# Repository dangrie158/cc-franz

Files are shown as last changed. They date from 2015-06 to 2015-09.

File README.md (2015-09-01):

#Camera Control 
##--> iPad controlled camera slider <--

<br /><br />
###Who we are
Hi, let’s introduce ourselves first: we are [Daniel Grießhaber](https://twitter.com/DanielGriehaber) and [Tobias Schneider](https://twitter.com/hpppxl), two master students (Computer Science and Media) of the Stuttgart Media University.

###TL;DR
Awesome, selfmade Camera Slider for ~180€ that can be controlled and programmed via an iPad app. If you read along you will find information on how to build one yourself!

###What this is
During the summer term of 2015 we developed a Camera Slider for controllable and repeatable time lapse and realtime shots. Since there are [already a couple DIY sliders](http://hackaday.com/2014/01/27/yet-another-diy-camera-slider/) out there, we wanted to give ours some special features to make it stick out from the masses:

###Awesome feature list:
#####2 motorized axis (linear movement and panning)
Most DIY Camera Sliders out there have only one remote axis. We have two (more is always better). ;-)
#####WiFi Access
Thanks to some recent development in WiFi integration we were able to add an iPad to control the Camera Slider.
#####iPad Control
There are two ways of controlling the Camera Slider. First of all, you can handle the slider via the live control and steer both axis independently. Furthermore, you can record your movement and save it for later playback.
 
Secondly, you can create simple scripts over an intuitive, graphical UI to program the slider for long duration shots (e.g. time lapse) with a slow, smooth and continuous movement that is repeatable until you are happy with the outcome.

## TOC

* [Mechanical Engineering](Slider/CAD/)
* [Electrical Engineering](Slider/Mainboard/)
* [ESP8266 WiFi Module](Slider/WiFi-Module/)
* [Microcontroller](Slider/Firmware/)

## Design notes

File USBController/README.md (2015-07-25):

# cc-franz
This is part of the CC-Franz Project

Implemented by Stefan Seibert at Stuttgart Media University in Summer 2015
as part of the class "Embedded Systems" from Thomas Maier.

You will find two subfolders:

/USB-Shield
This subfolder contains the AVR based project code to use the
USB Host Shield with MAX3421 chip in combination with a AVR
ATmega328p without the need of the Arduino Development Framework.
The Code can be compiled with AVR-GCC by using the provided makefile.
It is configured to send the Input Data of a HID Gamecontroller via UART

Files in USB_Shield originated or extended from Stefan Seibert, comments in files also:
/utils.h + /utils.c - For sending data or debug information via UART
/usb_wifi.cpp - main file, for initiation of USB Protocol and sending commands
/hidjoystickrptparser.h + /hidjoystickrptparser.cpp - modified and extended to handle input correctly

/WebSocket_Client
this is the firmware for a websocket client for the ESP8266 WIFI module
It needs the esp_open_sdk (https://github.com/pfalcon/esp-open-sdk) 
for being compiled correctly. It can be compiled to flash the ESP8266.
It is configured to send the via UART received USB Control Data 
as WebSocket Messages.

Files in WebSocket_Client originated from Stefan Seibert, comments in files also:
/user/user_main.c - firmware main file for creating a HTTP Server in ESP8266
/user/websocketd.h + /user/websocketd.c - For creating a Websocket Connection as Server extended
from a old version from Daniel Grießhaber where WebSocket worked as client not as server.

HID Based Game Controller
=====================

Used Data for Events:

X = 1 A = 2 B = 3 Y = 4  L = 5 R = 6 Select = 9 Start = 10
Kreuz Links: Z2 = 0 Kreuz Rechts: Z2 = 255 
Kreuz Oben: Rz = 0 Kreuz Unten: Rz = 255
Start = Rotation und Move auf 0 
Kreuz links/rechts = Move -/+ 
Kreuz hoch/runter = Rotation -/+  

A = Move Speed 255/8
B = Move Speed 255/2
Y = Rotate Speed 255/8
X = Rotate Speed 255

L = Speed -2 R = Speed +2

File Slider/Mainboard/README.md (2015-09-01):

###Electrical Engineering

#####BOM (What you need)

| Qty | Device | Package | Value  | Parts | Description |
|-----|---|---|---|---|---|
| 2 | A4988 | DIP | – | U3, U4 | |
| 1 | ¼W Resistor | 0207 | 100 kΩ | R15 | |
| 1 | Potentiometer | CA9V | 100 kΩ | R16 | |
| 8 | Ceramic Capacitor | C050 | 100 nF | C1, C2, C4, C5, C6, E13, E14, E15 | |
| 2 | Electrolytic Capacitor | CA9V | 100 µF | C4, C8 | |
| 5 | ¼W Resistor | 0207 | 100 Ω  | R3, R4, R10, R11, R12 | |
| 8 | ¼W Resistor | 0207 | 10 kΩ  | R1, R2, R5, R6, R7, R8, R9, R14 | |
| 2 | Electrolytic Capacitor | CA9V | 10 µF  | C3, C16 | |
| 1 | Power Check | – | – | JP1 | |
| 1 | Crystal Oscillator | HC49 | 16 MHz | Q1 | |
| 1 | Diode | DO41 | – | D2 | |
| 4 | Electrolytic Capacitor | CA9V | 1 µF | C9, C10, C11, C12 | |
| 2 | Ceramic Capacitor | C050 | 22 pF  | C17, C18 | |
| 1 | LM33CV | TO22 | – | IC2 | |
| 1 | 8705 | TO22 | – | IC1 | |
| 1 | Atmega328P | DIL28 | – | U1 | |
| 2 | BC337 | TO92 | – | T1, T2 | NPM Transistor |
| 1 | 2 Pole Connector | – | – | IROUT | |
| 1 | 3 Pole Connector | – | – | ENDSTOP | |
| 3 | 4 Pole Connector | – | – | MOT1, MOT2, RS232 | |
| 1 | 2x3 Pin Header | – | – | ICSP | |
| 2 | 3 Channel DIP switch | – | – | MSMOT1, MSMOT2 | |
| 1 | ESP8266 | – | – | U5 | |
| 1 | LM358 | DIL08 | – | IC3 | jelly bean Opamp |
| 1 | MAX232 | DIL16 | – | U2 | |
| 1 | 5mm LED | – | – | D1 | |
| 6 | Tactile Button | – | – | HOMING, LEFT, RIGHT, TILTCCW, TILTCW, RESET | |

Total costs for electrical parts: <br />
**~ 39,33€ + shipping fees**

#####Schematic
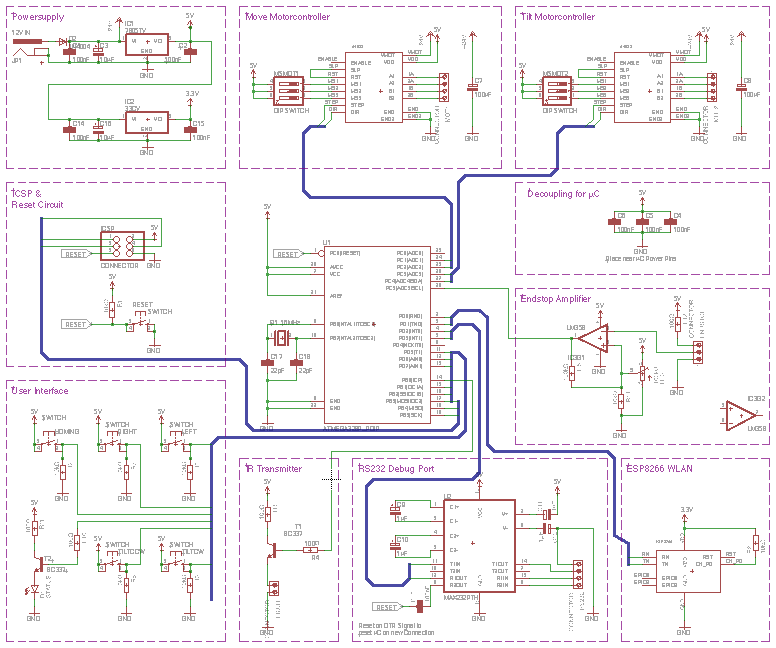
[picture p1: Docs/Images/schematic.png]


We designed the schematic modular to get a good overview of the whole system and work independently on single modules. 

######Microcontroller (not labeled, the part in the center)
For the brain of our slider we’ve chosen an ATMEGA 328 from Atmel. The reason for this simply was the huge amount of information and tutorials out there for this chip. This is the same chip you have on the Arduino Uno, the one you may have in your parts bin.  Just for kicks (and maybe also because this was a requirement by our lecturer) we did not use the Arduino bootloader or libraries and programmed the chip directly through the ISP interface. <br />
The chip has an whopping 32kB of Flash and 2kB of RAM.

######Powersupply
For the operation of the Camera Slider we need 3 different voltage rails: +12V for the motors, +5V for the microcontroller and as a main logic level and +3.3V as the WiFi module supply voltage.<br />
The +12V line is directly connected to the main power jack, which is supplied by an external plug pack. The +12V are only fed through a diode to protect the circuit from reverse polarization, which results in a small voltage drop of about the typical 0.7V.
For the +5V a linear 7805 voltage regulator was used, which turns any input voltage from +7V - +35V into a regulated +5V. The aforementioned is accomplished by burning all the extra energy and turning it into heat. During normal operation our slider consumes about 300mA on the +5V rail and therefore the energy of



heat needs to be dissipated. For that reason we attached a small heatsink to the voltage regulator. <br />
The 3.3V rail is also regulated by a linear regulator, but this time with another output voltage. The input voltage comes from the +5V line, which means that the 7805 needs to supply the current for the +3.3V rail as well. However, directly attaching the regulator to the 12V would mean that it needs to dissipate all the power down to the 3.3V, wich would result in a drop voltage of 12V - 3.3V = 8.7V. This way, the heat is spread across the two regulators.

######ICSP & Reset Circuit
The ICSP connector is needed to program the ATMEGA microcontroller. It is a simple SPI bus with power supply and a connection to the RESET pin of the controller. To flash the controller, the programmer needs to set the RESET pin low and therefore keeps the microcontroller in its reset state during the flashing process. To start the microcontroller, one needs to keep the RESET pin high. For this reason the RESET pin is connected to the 5V rail with a 10kΩ pull-up resistor. <br />
For manually resetting the controller, we also added a switch to pull the pin low. 

######Motor Controller (x2)
To drive the motors, we used 2 A4988 motor drivers. They handle all the complex driving and enable us to microstep the motors, which results in an up to 16x higher resolution to drive the motor. <br />
The microstepping setting is not subject to change during operation. However, to be able to set the bits manually we simply added a 3 pole DIP switch to each driver which allows us to change the setting after laying out the board.<br />
One could also hard-wire the setting in the same board layout by not populating the switches, but solder in the connections directly.
The microcontroller can make the motor step (or microstep) by toggling the STEP pin of the controller for at least 1µs. The changing edge (HIGH to LOW or LOW to HIGH) doesn’t matter. The direction of the motor is controlled by setting the DIR pin HIGH or LOW.

######Endstop Amplifier
Designing the mechanical construction, we realized that it would be nice to detect a special position of the linear axis to have a known reference point we could align the axis reference system to. Of course, the simplest way to implement such a feature would be a simple switch with a small lever which gets pressed when the axis moves past a threshold at the end of the axis. However, the simplest solution always is the most boring solution, and since this is a project where we wanted to learn something, we have chosen a more sophisticated and nicer way instead.
The solution should be opto electrical by using a photocell to detect the threshold position. The output of the photocell is analog and we quickly realized that photocells are not very stable in variable lighting conditions, and since we wanted to be able to use the slider during day- and nighttime we needed a way to amplify the cells return value. <br />
To convert the analog signal into a digital, binary one, we could have used a schmitt trigger with a matching threshold voltage, but back then we did not know what this threshold voltage would be. For this reason we implemented the schmitt trigger using an opamp and a precision 10 turn resistor to set the threshold.

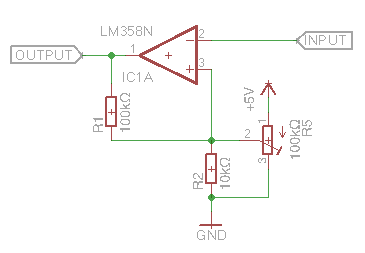
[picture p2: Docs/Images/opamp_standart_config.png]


The LM358 is used in inverting amplification mode. While the voltage at the negative (inverting) input of the opamp is lower than the voltage at the positive (non-inverting)  input, the opamp drives its output high. <br />
R1 is the feedback resistor that mixes the output signal back into the non-inverting input. R2 and the variable resistor R5 form a voltage divider which sets the voltage of the non inverting input (ignoring the feedback for a moment). The voltage at the input of the opamp 

.

If we now assume that the variable resistor is set to e.g. 10kΩ, we can calculate an input voltage of

.

That’s our basic threshold. Now we assume that the voltage at the inverting input (this is the output of the photo cell) is lower than this threshold, let’s say 1V. The opamp now drives its output high. <br />
Now we basically have a voltage of 5V at the output of the opamp. We can simplify the circuit in this state into the following one:

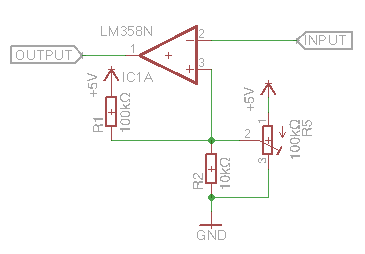
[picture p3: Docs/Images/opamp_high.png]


As one can see, we simply connected R1 directly to 5V instead of the output. When you look closely , we have R5 and R1 now in parallel, we can see this more clearly if we move R1 next to R5:

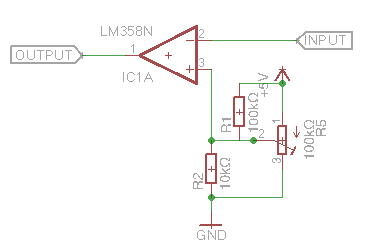
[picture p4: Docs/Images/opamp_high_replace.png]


Since R5 and R1 are now in parallel, we can simply replace them by a single resistor (assuming R5 would still be set at 10kΩ) with the value:

.

This changes the threshold because the ratio between the two resistors changed. The threshold is now at

.

As we can see, our threshold voltage was raised, which means our trigger actually triggers at 2.62V. <br />
Now, let’s assume the voltage at the inverting input to our amplifier is raised above those 2.62V. The opamp instantly drives the output low. We, once again, can present this state as an equivalent circuit diagram:

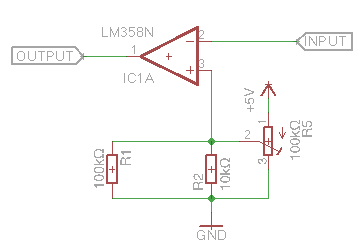
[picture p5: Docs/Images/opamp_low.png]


You can clearly see that R1 and R2 are now in parallel. We can calculate the resistance they have as

.

That’s of course the same value we calculated for the other state. The interesting thing, however, is that we now have another threshold voltage. We can calculate it as

.

This means we have a hysteresis area of

.

This means the amplifier outputs a high signal as soon as the input signal reaches at least 2.62V, but only goes low again, if the input drops lower than 2.38V. Without this hysteresis through the feedback resistor R1, the amplifier could oscillate if you apply exactly 2.5V to the input. <br />
Since R5 is a variable resistor, the threshold voltage of the amplifier can be set to almost anything between 0 and 5V, even after the board is assembled. You can do the math for any other value of R5 now.

######WiFi Module
The WiFi Module we used is the ESP8266 Chip on a breakout board. This chip has received a lot of attention already, because it is available for ~3€ each. This is ~86€ cheaper than the [official arduino wifi shield](http://www.amazon.de/Arduino-WiFi-Shield-Smart-Projects/dp/3645651985). With the shipped firmware, this chip is controllable over an AT command set over a serial RS232 connection. However we later changed the firmware with our custom one. To communicate with the main ATMEGA, however, we still used a RS232 connection.

######RS232 Debug Port
To debug the firmware we wanted a serial port just to write debug messages and states. Since the ATMEGA only has one hardware serial port we just connected the debug module of the schematic to two random pins and used the hardware serial port for the communication with the ESP8266. <br />
Today, everybody uses the RS232 protocol at TTL levels (0V-5V) with dupont wire. However, the original standard uses a [DB-9 connector](http://www.electronicsplanet.ch/Anschl/seriell.html) and logic levels of -/+15V. We wanted to stick with the original standard and for that reason, we needed to convert the TTL signal to the full +/-15V swing. The chip that accomplishes that is the [MAX232](http://www.ti.com/lit/ds/symlink/max232.pdf). The nice thing about it, is that it does not need a positive and negative 15V rail to generate the signals. It instead uses a charge-pump and is therefore lucky with a supply of 5V. If you can’t get bothered to use the old standard and do not plan to connect the controller to the com port of an old computer, you can simply not populate the capacitors C9-C12 and the MAX232 chip U2. The simply bridge the pins from the micro directly to the debug connector.

######IR Transmitter Driver
Most cameras have the ability to control the shutter over a simple infrared camera. Although most vendors sell the remote control as a separate product, the IR codes for most cameras are readily available in the internet. Just to be able to control the shutter, we added a jelly bean BC337 NPN transistor to drive the LED. The transistor to drive the LED is probably not necessary because the ATMEGA can source ~20mA and sink ~40mA from its I/O ports which should be more than enough for most modern LEDs. However, it would be to drive the LED directly and transistors are not that expensive. Again, if you don’t want the driver, you can simply not populate it.

######User Interface
For test reasons, and to be able to control the slider without having an iPad at hand, we implemented a user interface with five buttons. These buttons allow you to control the angular and linear axis of the slider. The fifth button did not have any meaning back then, but is now used to start a predefined script. Furthermore, every button can be used to toggle the LED for feedback purposes. <br />
We used external pulldown resistors although the ATMEGA has internal ones for all I/O pins. We’ve decided to use external ones because it is easy to lay traces underneath them. It would also be possible to replace the resistors R5-R9 with simple copper wire and use the internal pulldowns.

######Layout

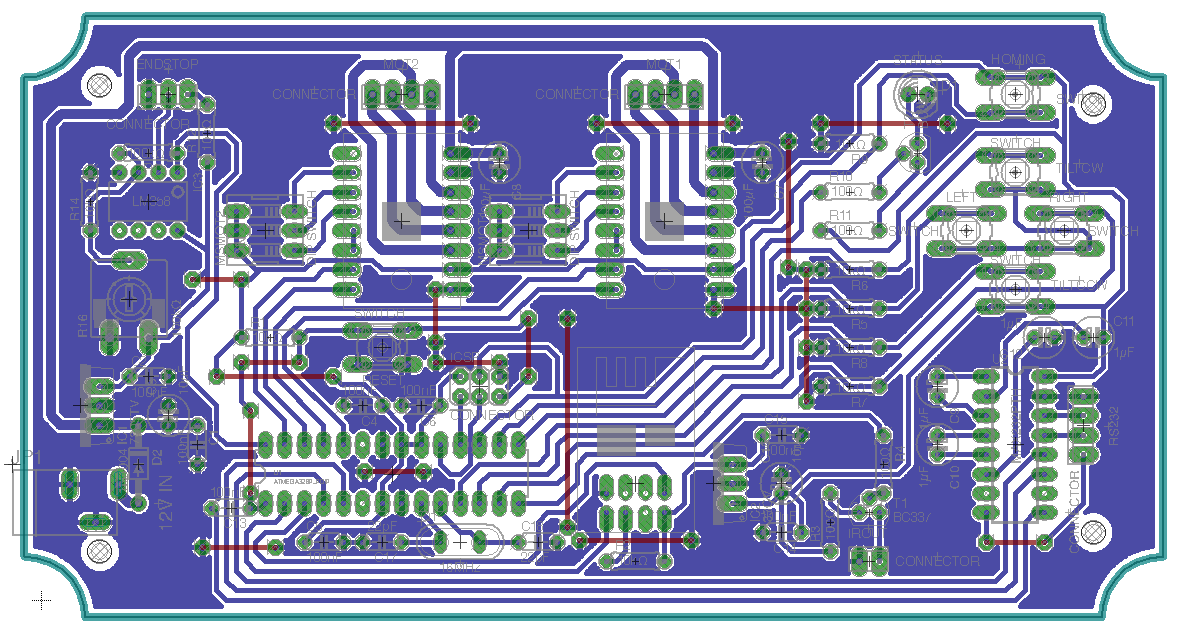
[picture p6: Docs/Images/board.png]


The board should be milled on the CNC machine we also used for the aluminum parts. For this reason we tried to lay out the board single sided just because it is much easier for home production. We ended up using 18 jumper wires, which is a pretty good end result. If you don't have a CNC mashine and don't want to install eagle, we have a black and white version of the layout for etching [here](https://github.com/dangrie158/cc-franz/raw/develop/Docs/Pdf/mainboard_etch.pdf).

The general layout uses the same modular setup we designed into our schematic. Since we do not need any high speed data transmission lines, the board is rather simple and there were not many potential problems. However, some things we kept in mind include:

######Local regulation and power traces
You should avoid running your power traces across the whole board, just because the copper also has a resistance. This resistance is higher, the narrower and longer the trace is. For this reason, the high current +12V power traces for the motor supply are 50 mil wide and are kept as short as possible, thus the power jack is quite close to the motor controllers. <br />
Another problem is that a higher trace resistance means a higher current for the rail because the resistance needs to be overcome. For this reason, the regulation should always happen as close to the device as possible. This also reduces ripple on the trace from coupling with other digital I/O lines. Our 5V rail is needed all over the board, so there is not much we can do to optimize in this respect. The 3.3V rails, however, is only needed for the ESP8266 WiFi Module and thus the LM33CV regulator is placed right next to it.

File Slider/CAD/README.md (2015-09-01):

###Mechanical Engineering
with eBay links – no affiliate, we do it all for love

#####BOM (What you need)
(inches are rounded to the closest fraction, everything was ordered in mm)

| Qty | Name | Dimensions | Price |
|-----|---|---|---|
| 2 | [aluminum sheet](http://www.ebay.de/itm/Alublech-1-5-mm-Aluminium-Tafel-Aluminiumlech-Alu-Zuschnitt-Grose-wahlbar-/111703985176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) | 300mm x 200mm x 2mm – 11¾ in x 7¾ in x 80 mils | ~ 2,39€ pc. |
| 2 | [linear bushing](http://www.ebay.de/itm/SC8UU-SCS8UU-Linearlager-Linearwagen-Linearschlitten-Linear-Motion-Ball-Bearing-/351361591099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) | | ~ 3,45€ pc. |
| 2 | [linear shaft](http://www.ebay.de/itm/Prazisionswelle-8-mm-100-990mm-wahlbar-17-m-Tol-h6-geschliffen-cf53-1507-/390374537633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) | 600mm x ∅8mm – 23⅔ in x ∅8mm | ~ 10,20€ pc. |
| 4 | [shaft holder](http://www.ebay.de/itm/Wellenhalter-SH8-SH10-SH12-SH20-Welle-Linear-Rail-Shaft-Industrie-CNC-/151237551016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) | ∅8mm | ~ 3,30€ pc. |
| 1 | [aluminum profile](http://www.ebay.de/itm/ALU-Profil-Aluprofil-30x30-Nut-8-Profile-Aluminium-AlClipTec-/381199654414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) | 30mm x 30mm x 400mm – 1⅛ in x 1⅛ in x 15¾ in | ~ 2,76€ pc. |
| 1 | [jointed arm](http://www.ebay.de/itm/Gelenk-mit-Klemmhebel-fur-30x30-Aluprofil-/260979085629?hash=item3cc390d13d) (for camera attachment) | 30mm x 30mm – 1⅛ in x 1⅛ in | ~ 16,90€ pc. |
| 2 | [stepper motor](http://www.ebay.de/itm/Schrittmotor-Stepper-Motor-Nema17-42BYGHW811-4800g-cm-2-5-A-3D-Drucker-RepRap-/261825775758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) | | ~ 14,90€ pc. |
| 4 | [stands](http://www.ebay.de/itm/4x-Gelenkstellfusse-Stellfusse-fur-30x30-40x40-Alu-Profil-Aluprofil-Stellfuss-/291379384790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) | M8 | ~ 3,22€ pc. |
| 1 | [GT2 belt](http://www.ebay.de/itm/Riemen-GT2-Open-Belt-Meterware-Zahnriemen-3D-Drucker-CNC-RepRap-/171898713404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) | 1m - 40 in | ~ 2,20€ pc. |
| 2 | [GT2 pulley](http://www.ebay.de/itm/Zahnrad-Pulley-GT2-20-Zahne-fur-5mm-Welle-CNC-RepRap-3D-Drucker-Prusa-/181838550576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) | | ~ 2,90€ pc. |
| 1 | [small turntable](http://www.ebay.de/itm/Drehteller-70x70mm-Drehlager-Drehtablett-Drehplatte-Flanschlager-Druckkugellager-/131458159153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) | 70mm x 70mm - 2¾ in x 2¾ in | ~ 2,58€ pc. |
| | Nuts and bolds | (M8, M6, M4, M3 and probably a couple more..)  | ~ 20€ |
Total costs for mechanical parts: **~ 138.20€ + shipping fees**

#####Machining the parts
To connect all the parts we used the 2mm sheet metal. Since we had access to a CNC milling machine, we created CAD drawings for most of the parts. All holes are included in the drawings, however if you are missing small enough end mills, like we did, you might have to drill some of the holes manually. It comes in handy to print the drawing at 100% final scale and tape it on the milled part using scotch tape. This way, you can use the marked centers to spot the holes before drilling.

Every drawing requires to be milled one time.
The only parts not available as a drawing are the two aluminum profile sides, where all the plates are attached to. The drawings are currently optimized to a 160mm wide slider. If you want a broader slider to get a little more stability, you need to modify the bottom side of the turntable fixture first.

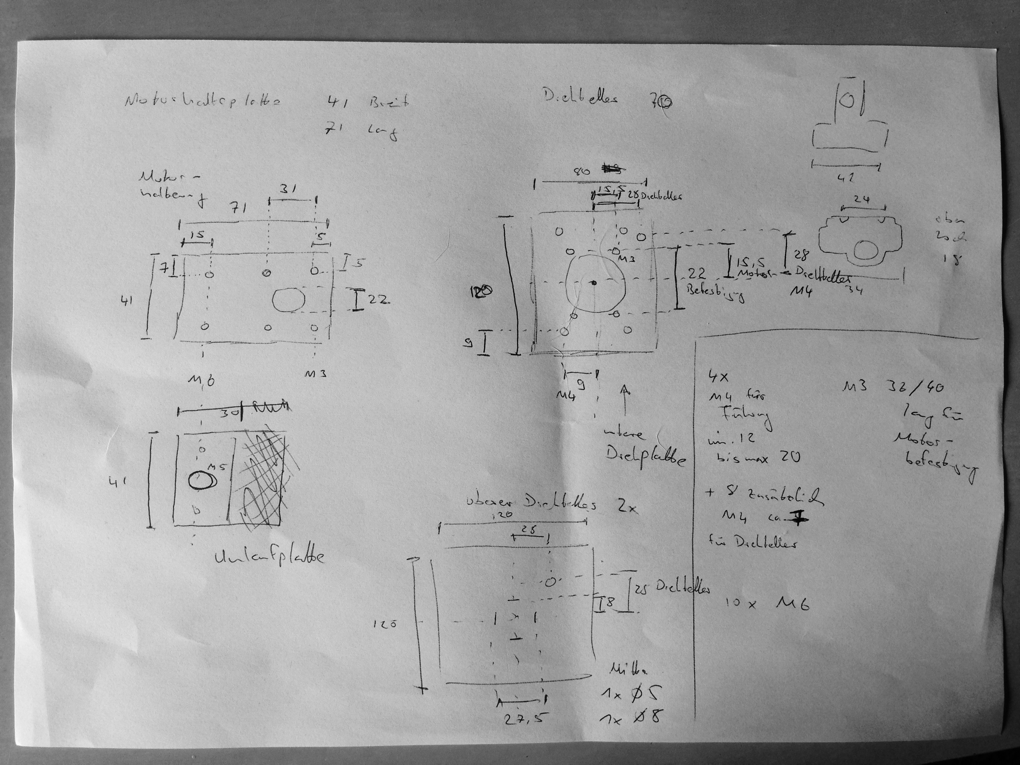
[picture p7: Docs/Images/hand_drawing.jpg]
Hand Drawing


#####List of Drawings

| Name | Description |
|---|---|
| motor attachment.dwg | attachment for a Nema17 motor, for the linear axis |
| pulley attachment.dwg | attachment for a GT2 pulley, as the other side of the linear axis motorization |
| turntable fixture bottom.dwg | attachment for the 2 SCS8UU linear bushings and the bottom side of the turntable |
| turntable fixture top.dwg | attachment for the top side of the turntable |
| motor attachment.dwg | the topmost layer used to attach the jointed arm |

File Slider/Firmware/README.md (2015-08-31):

###Microcontroller

#####Setup
When the microcontroller boots up, it sets up its GPIO pins as input or output and writes the initial values to them.<br />
After that the hardware UART is configured to async receive mode at 9600 baud. This is the UART that is connected to the WiFi module.<br />
Following along, the 16 bit Timer 1 is set up to fire an interrupt at 1kHz.

#####Main Loop
In the main loop are basically 4 tasks happening:
* check the UI buttons and handle them if they are pressed
* check if the UART received a whole line and parse it
* handle the hard coded script if it was previously started by the UI
* check if the position of the slider has changed and send an update via UART if needed

#####Communication Protocol
The whole protocol is based on WebSockets. Clients can send masked payload to the server. Control messages have the following format:

```
<axis><direction><speed>
```

where:

* `axis` is either 'M' or 'R' as single char
* `direction` is either '+', '-' or '0' where '0' stands for STOP
* `speed` is an integer 00-FF which is sent as hex

Examples:
* `M+75` – move slider with speed 75 to the right
* `R+65` – pan slider with speed 65 clockwise
* `R0` – stop the panning
* `M-10` – move the slider slowly to the left

To avoid heavy parsing each message should only contain the specified letters and no spaces or other characters whatsoever. Each message is followed by a single `\n` newline (no `\r`)

Further special messages that can be sent are 
* `ZM` or `ZR` – set the axis current position as 0 reference (movement and rotation)
* `HM` or `HR` – tell the slider to automatically move to its 0 reference (homing)

Last but not least, the slider is not only able to receive messages from an iPad, but send them to it. This way it is possible to tell the iPad the current position of the linear and angular axis via the following messages:
* `PMFFFF` - With FFFF being a hexadecimal position
* `PRFFFF` - With FFFF being a hexadecimal position

#####Message Parsing
The messages are sent by the WiFi module over UART and are parsed by the microcontroller. The parsing routine is rather simple:
* Read the first byte from the message
* Is it a M, R, Z or H, take a look at the next byte, else just drop the message
* Parse the second byte with respect to the previous byte 
* If the first byte was a M or R, and the second byte was not a 0, use the strtol with a base of 16 to parse the hexadecimal number that should be there. Since the string that is parsed is null terminated explicitly while reading the uart buffer, this is a save function even if strtol has no maximum length parameter like strncpy.

The parsing of the message is done in every cycle of the main loop if the UART has read a line.

#####Reading lines from the UART
The UART is, as already mentioned, configured in asny receive mode, which means it triggers an interrupt every time a byte is read. We don’t really care about single bytes, we want the whole line. For this reason we moved all the UART functions to its own files `uart.c` and `uart.h`. In these files we handle the interrupt and save the newly received byte in a line buffer of a maximum length of 100 bytes. This limit is more than enough for our simple message format. If the limit is reached before the end of the line is detected (CR or LF), the buffer is cleaned. This protects the system from a buffer overflow while reading the string. If the received buffer is either a `\n` or `\r` character, the line is considered complete and the string buffer is terminated with a `\0`. Since this all happens within the interrupt context of the hardware uart, we simply set a flag to indicate that the string is now ready for consumption. This flag is checked in the main loop while parsing the messages. If the main loop is ready parsing the message, it clears the flag and therefore indicates that the string is ready to be overwritten.<br />
Since both, the string buffer and the flag, are used in an interrupt and a main context, these variables need to be defined volatile or else the compiler may would optimize the access to them. By declaring them volatile we tell the compiler that it can not know when or if the variable will change.

#####UI and Motor Control
Performing a step with either motor means setting the STEP pin for the controller high for at least 1ms, then setting it low for at least 1ms before performing another step. The 1ms is used to set the maximum speed of the motors. We noticed that this is a good compromise between speed and stability, because if you drive the motors too fast, they may miss some steps.<br />
Each pass of the main loop, all buttons of the UI are checked. If any button is detected to be pressed (reads a high value), a step in the corresponding direction is performed.

#####Timer
As said, Timer 1 is used to fire an interrupt at 1kHz. This static interval is necessary because we need a way to calculate if we have to perform a step into any direction within this loop. Let’s say we receive and parse a message that states we should drive to the right with a speed of 15%. Since our main loop runs at no fixed interval, there is no way we could decide if we should perform a step within this run. If the user presses a button, the main loop automatically needs 2ms longer to perform the motor step. By using the timer we have a fixed interval to calculate if we need to perform a step each n-th interval to get the desired speed.<br />
Since our Timer runs an interrupt, and you should never wait or do any long running task in an interrupt context, we cannot simply do the toggle-wait-toggle-wait routine like we do when handling the UI. Instead we just use a counting variable which we increment every time we run the function to check if we waited long enough to perform the next step.

#####Software UART
To debug the Firmware, it is always nice to have a simpler way than toggling an LED. Text, for example, is great for this purpose. You can send values of variables, markers where you are in the execution and so on. <br />
For this purpose we added a second serial port to our project. Sadly, the ATMEGA only offers one hardware UART. Therefore, we needed to emulate one. Since we did not need to receive anything from the port, the task was rather simple. Receiving is kind of hard, because RS232 is asynchronous and has no clock. For this reason, it is critical to notice when a byte starts and then check the logic levels on the line every 1/BAUD_RATE seconds. You can do this with pin change interrupts and a timer, but it gets rather complicated. For sending you can just bit bang the byte synchronously with delays. 



You start to transmit a bit by pulling the line low for a bittime. After that, you start transmitting the byte bitwise starting with the least significant bit and waiting a bit time before the next bit. After transmitting the most significant bit, you pull the line high again for the stop bit. After that, you can transmit the next byte by sending a start bit first.

 is is the bit time and is equal to



This method can be easily implemented using the `avrlib __delay_us()` function and simple I/O which we did in `debugSendByte()`.

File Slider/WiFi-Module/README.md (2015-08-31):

###ESP8266 WiFi Module
The ESP8266 is a Xtensa LX106 Microcontroller with an integrated 802.11x WiFi transceiver. It has an integrated TCP stack and therefore provides a good abstraction layer.<br />
With its standard Firmware, the communication happens over a simple AT Command interface over a serial UART. With this interface the use of the chip is very limited.

#####Why WebSockets
We wanted to use WebSockets as the communication protocol on top of TCP. This leaves us with the option to create a web based control interface for the slider, although this is not planned in the near future. There are also WebSocket libraries available for almost any language. Furthermore, websockets are fast and lightweight, so virtually perfect for the use in an embedded environment. Sadly, there is no ESP8266 firmware out there that supports WebSockets, but since we are both software developers this should be nothing to worry about.<br />
Basically we want the ESP8266 Chip to be responsible up until the WebSocket protocol. The communication should still happen over the UART interface. If the module receives a WebSocket message, it unpacks the payload and writes it out over UART. If it receives a line (terminated by CR&LF), it creates a new WebSocket frame and sends it to all its clients.<br />
The module also acts as a WebSocket server that opens a WLAN access point clients can connect to. This is important because it is impossible to create a WLAN with an iPad.

#####WebSocket protocol
The WebSocket protocol is rather simple: 
* The client sends a HTTP request to the server with the headers ‘Connection: upgrade’ and ‘Upgrade: websockets’ set. Furthermore, a random 32byte key, the ‘Sec-Websocket-Key’,’ is send within the headers.
* The Server calculates the answer to the ‘Sec-Websocket-Key’:
*  it concatenates the WebSocket GUID ‘258EAFA5-E914-47DA-95CA-C5AB0DC85B11’ to the original key
*  it calculates the SHA1 hash of the result
*  it Base64 encodes the hash
* The server sends the response with the status code ‘101 - Switching Protocols’ and the calculated key

After this sequence the TCP connection is ready to transmit WebSocket frames. This whole routine happens in the `wsRecvCb `callback in the code. The key is calculated in `createWsAcceptKey`. <br />
WebSocket frames are in a simple binary format that is described in the header file `websocketd.h`. The description is basically a copy of the [RFC 6455](https://tools.ietf.org/html/rfc6455). The parsing of the received frames and the sending happens in `parseWsFrame` and `sendWsMessage` respectively. <br />
The main loop happens in `user_main.c` which starts the WebSocket server, registers a callback for new messages and reads the UART.

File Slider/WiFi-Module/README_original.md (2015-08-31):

Websocket Daemon for the ESP 8266
=================================

This is a Websocket implementation based upon the [RFC 6455](https://tools.ietf.org/html/rfc6455).

The Library uses a stripped Version of the [esphttpd](http://git.spritesserver.nl/esphttpd.git/) as a base. Even though the Websocket Implementation is fully independent from this code, I used this Project as a starting point. So thanks to the author os this project.

The code implements a WebSocket Deamon for the ESP8266 WiFi Module. It supports:

* listening for new Clients
* doing the handshake 
* Sending and receiving messages
  * as plain text
  * as binary
* message unmasking
* creating arbitary message frames
* callbacks for received messages

ToDo:

* connect to servers
* send as client

There are no direct dependencies, as a SHA1 and a Base64 implementation are part of the code.

Sample server that just echoes ws frames on the UART (serial)
-------------------------------------------------------------

```c
void onWsMessage(WSConnection *connection, const WSFrame *message) {
    for (int i = 0; i < message->payloadLength; i++) {
        stdoutPutchar(message->payloadData[i]);
    }
    stdoutPutchar('\n');
}

void onWsConnection(WSConnection *connection) {
    connection->onMessage = &onWsMessage;
}

//Main routine. Initialize stdout, the I/O and the webserver and we're done.
void user_init(void) {
    uart_init();
    ioInit();
    websocketdInit(8080, &onWsConnection);

    //Start os task
    system_os_task(rxLoop, RX_PRIO, user_procTaskQueue, RX_QUEUE_LEN);
    system_os_post(RX_PRIO, 0, 0 );

    os_printf("\nReady\n");
}
```

sample server that echoes the serial data (bidirectional)
---------------------------------------------------------

```c
#include "espmissingincludes.h"
#include "ets_sys.h"
#include "osapi.h"
#include "os_type.h"
#include "uart.h"
#include "websocketd.h"

#define RX_PRIO 0
#define RX_QUEUE_LEN 1
#define COMMAND_MAXLEN 1024

os_event_t user_procTaskQueue[RX_QUEUE_LEN];
static char *statusCommand = "STATUS:";
static uint8_t commandMatcher = 0;
static uint8_t commandMatched = FALSE;
static char command[COMMAND_MAXLEN];
static uint32_t commandPosition = 0;

//Main code function
static void ICACHE_FLASH_ATTR rxLoop(os_event_t *events) {

	int c = uart0_rx_one_char();

	if (c != -1) {

		if (commandMatched == TRUE) {
			if (c == '\n' || c == '\r') {
				broadcastWsMessage(command, commandPosition, FLAG_FIN | OPCODE_TEXT);
				commandMatched = FALSE;
				commandPosition = 0;
				commandMatcher = 0;
			}else{
				command[commandPosition++] = c;
			}

			if (commandPosition == COMMAND_MAXLEN) {
				commandMatched = FALSE;
				commandPosition = 0;
				commandMatcher = 0;
			}
		} else {
			if (statusCommand[commandMatcher] == c) {
				commandMatcher++;

				if (commandMatcher == strlen(statusCommand)) {
					commandMatched = TRUE;
				}
			} else {
				commandMatcher = 0;
			}
		}
	}

	system_os_post(RX_PRIO, 0, 0 );
}

void onWsMessage(WSConnection *connection, const WSFrame *message) {
	for (int i = 0; i < message->payloadLength; i++) {
		stdoutPutchar(message->payloadData[i]);
	}
	stdoutPutchar('\n');
}

void onWsConnection(WSConnection *connection) {
	connection->onMessage = &onWsMessage;
}

//Main routine. Initialize stdout, the I/O and the webserver and we're done.
void user_init(void) {
	uart_init();
	ioInit();
	websocketdInit(8080, &onWsConnection);

	//Start os task
	system_os_task(rxLoop, RX_PRIO, user_procTaskQueue, RX_QUEUE_LEN);
	system_os_post(RX_PRIO, 0, 0 );

	os_printf("\nReady\n");
}

```

For Build and upload instructions please refer to the `README.esphttpd` of the esphttpd author.

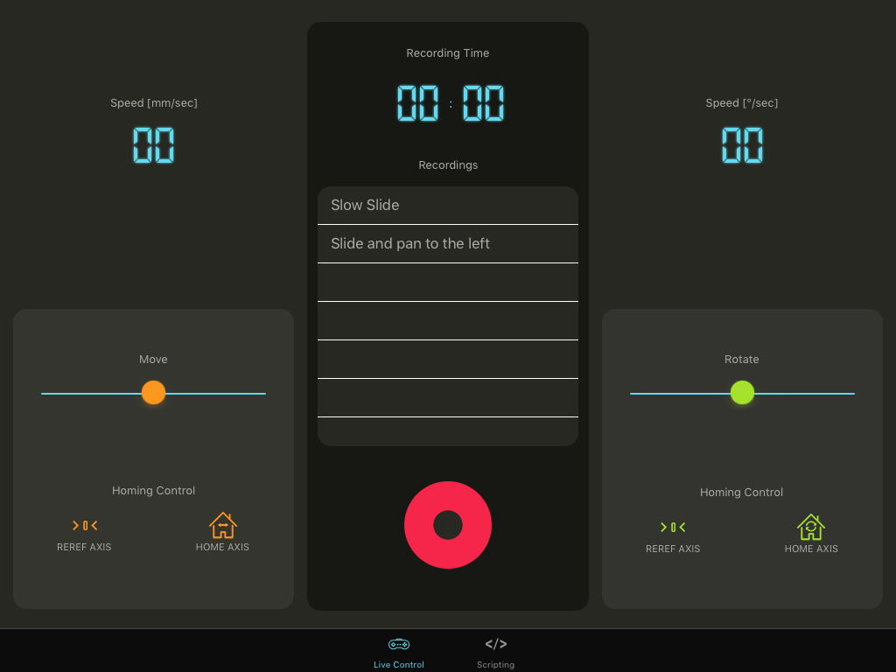
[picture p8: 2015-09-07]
Docs/Images/app_live_control.png

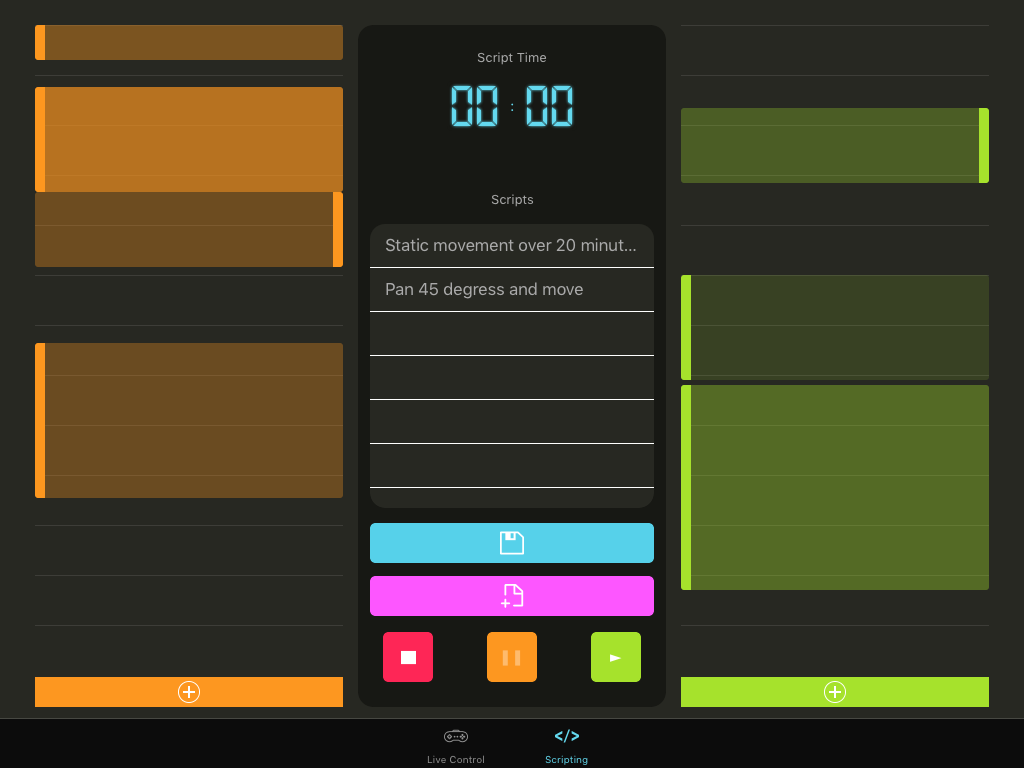
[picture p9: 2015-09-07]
Docs/Images/app_script_control.png

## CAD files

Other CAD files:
Slider/CAD/motorplate attachment.dwg
Slider/CAD/pulley attachment.dwg
Slider/CAD/camera attachment.dwg
Slider/CAD/turtable fixture top.dwg
Slider/CAD/motor attachment.dwg
Slider/CAD/turntable fixture bottom.dwg

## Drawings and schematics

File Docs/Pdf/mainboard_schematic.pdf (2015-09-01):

# GNDCONNECTOR

# GNDCONNECTOR

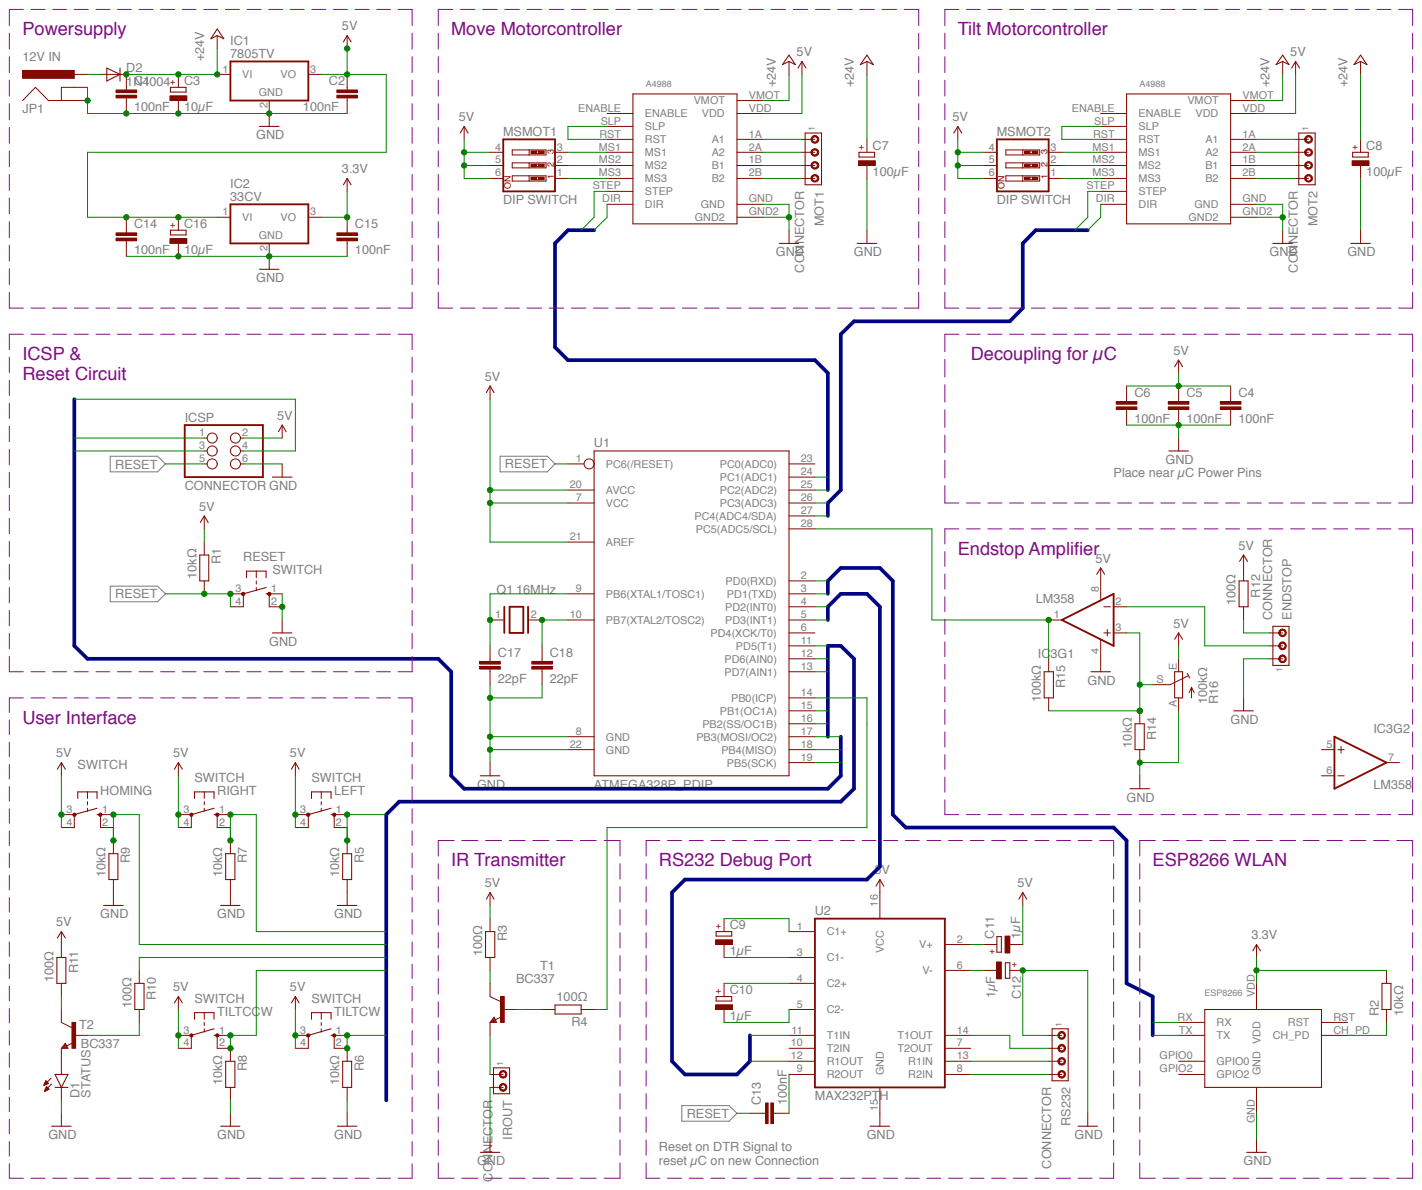
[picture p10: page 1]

Place near µC Power Pins

VDD VDD GND GND

Reset on DTR Signal to
reset µC on new Connection

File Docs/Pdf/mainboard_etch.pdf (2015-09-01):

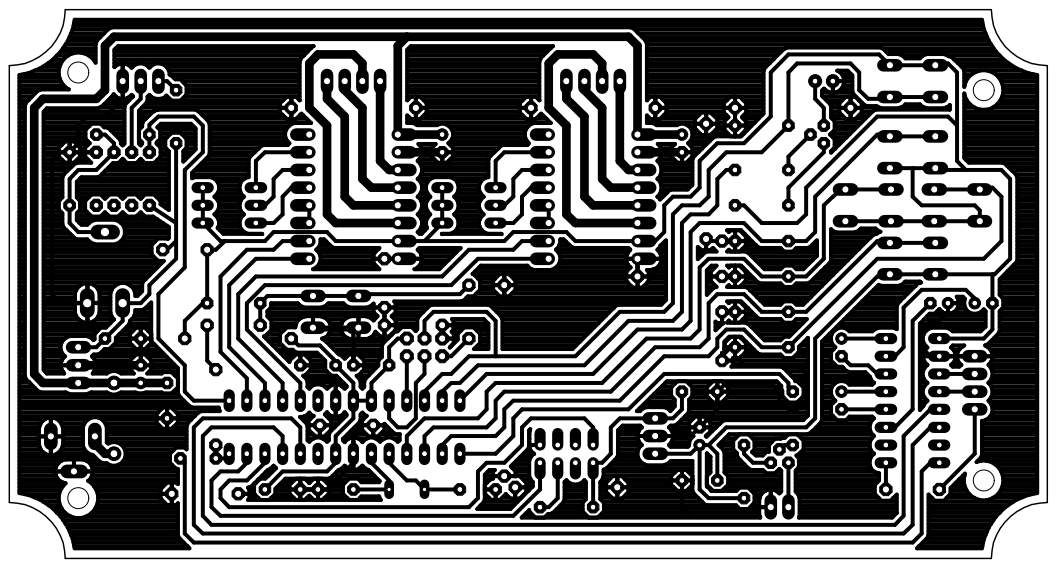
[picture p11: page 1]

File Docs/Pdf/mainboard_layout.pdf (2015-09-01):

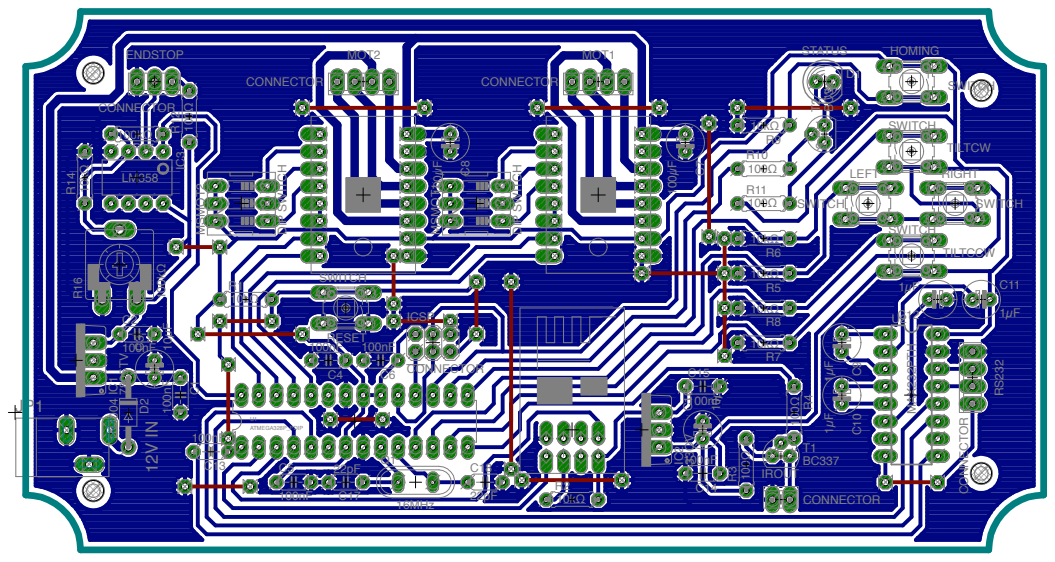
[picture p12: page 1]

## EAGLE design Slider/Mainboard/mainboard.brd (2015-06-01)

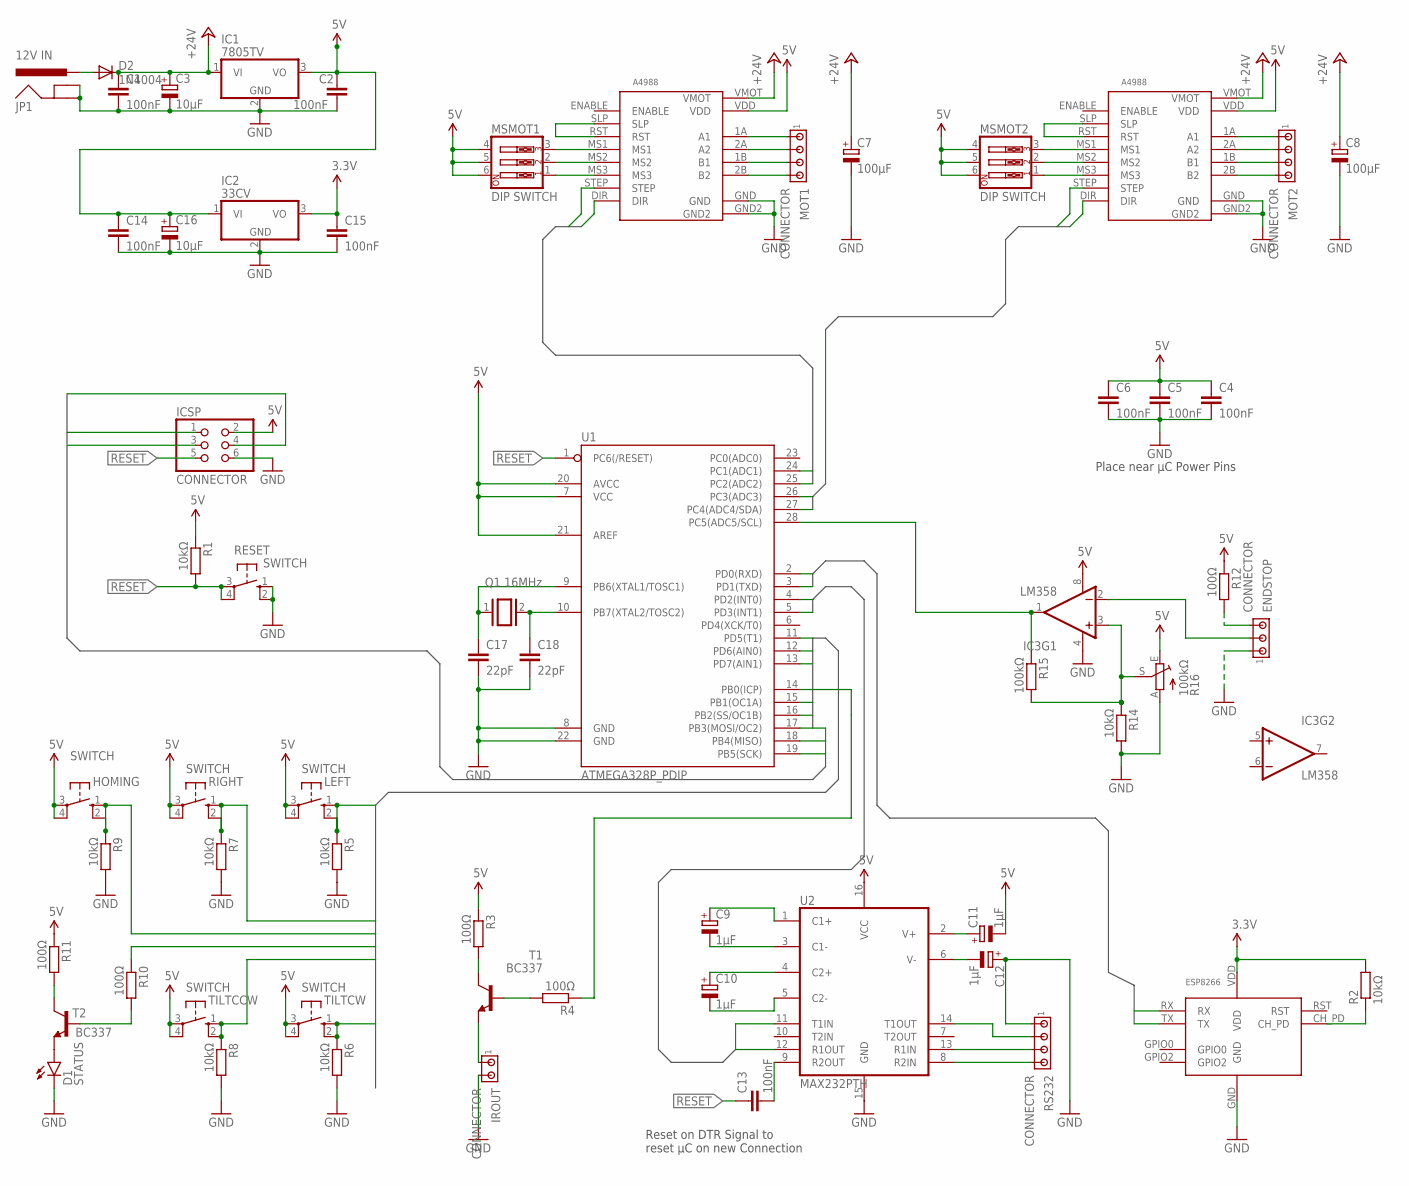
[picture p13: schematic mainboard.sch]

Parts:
C1, C2, C4, C5, C6, C13, C14, C15: 100nF; C050-024X044
C3, C16: 10µF; E2,5-6E
C7, C8: 100µF; E2,5-6E
C9, C10, C11, C12: 1µF; E2,5-6E
C17, C18: 22pF; C050-024X044
D1: STATUS; LED5MM
D2: 1N4004; DO41-10
ENDSTOP: CONNECTOR; 10X03MTA
HOMING: SWITCH; B3F-10XX
IC1: 7805TV; TO220V
IC2: 33CV; TO220V
IC3: LM358; DIP08
ICSP: CONNECTOR; 2X03
IROUT: CONNECTOR; 10X02MTA
JP1: 12V IN; POWER_JACK_SLOT
LEFT: SWITCH; B3F-10XX
MOT1, MOT2: CONNECTOR; 10X04MTA
MSMOT1, MSMOT2: DIP SWITCH; EDG-03
Q1: 16MHz; QS
R1, R2, R5, R6, R7, R8, R9, R14: 10kΩ; 0207/7
R3, R4, R10, R11, R12: 100Ω; 0207/7
R15: 100kΩ; 0207/7
R16: 100kΩ; CA9V
RESET: SWITCH; B3F-10XX
RIGHT: SWITCH; B3F-10XX
RS232: CONNECTOR; 10X04MTA
T1, T2: BC337; TO92
TILTCCW: SWITCH; B3F-10XX
TILTCW: SWITCH; B3F-10XX
U1: ATMEGA328P_PDIP; DIL28-3
U2: MAX232PTH; DIL16
U3, U4: A4988
U5: ESP8266

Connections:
3.3V: C15.1, IC2.3 (VO), R2.2, U5.VDD
5V: C2.1, C4.1, C5.1, C6.1, C11.-, C14.1, C16.+, HOMING.3, HOMING.4 (P1), IC1.3 (VO), IC2.1 (VI), IC3.8 (V+), ICSP.2, LEFT.3, LEFT.4 (P1), MSMOT1.4, MSMOT1.5, MSMOT1.6, MSMOT2.4, MSMOT2.5, MSMOT2.6, R1.1, R3.1, R11.1, R12.1, R16.E, RIGHT.3, RIGHT.4 (P1), TILTCCW.3, TILTCCW.4 (P1), TILTCW.3, TILTCW.4 (P1), U1.7 (VCC), U1.20 (AVCC), U1.21 (AREF), U2.16 (VCC), U3.VDD, U4.VDD
+24V: C1.1, C3.+, C7.+, C8.+, D2.C, IC1.1 (VI), U3.VMOT, U4.VMOT
DIR1: U1.24 (PC1(ADC1)), U3.DIR
DIR2: U1.26 (PC3(ADC3)), U4.DIR
ESPRX: U1.3 (PD1(TXD)), U5.RX
ESPTX: U1.2 (PD0(RXD)), U5.TX
GND: C1.2, C2.2, C3.-, C4.2, C5.2, C6.2, C7.-, C8.-, C12.+, C14.2, C15.2, C16.-, C17.2, C18.2, D1.K (C), ENDSTOP.1, IC1.2 (GND), IC2.2 (GND), IC3.4 (V-), ICSP.6, IROUT.2, JP1.GND@1 (GNDBREAK), JP1.GND@2 (GND), R5.2, R6.2, R7.2, R8.2, R9.2, R14.2, R16.A, RESET.1 (S), RESET.2 (S1), RS232.1, U1.8 (GND), U1.22 (GND), U2.15 (GND), U3.GND, U3.GND2, U4.GND, U4.GND2, U5.GND
HOMING: HOMING.1 (S), HOMING.2 (S1), ICSP.4, R9.1, U1.17 (PB3(MOSI/OC2))
LEFT: LEFT.1 (S), LEFT.2 (S1), R5.1, U1.11 (PD5(T1))
MISO: ICSP.1, U1.18 (PB4(MISO))
unnamed: U3.RST, U3.SLP
unnamed: MOT1.1, U3.1A (A1)
unnamed: MOT1.2, U3.2A (A2)
unnamed: MOT1.3, U3.1B (B1)
unnamed: MOT1.4, U3.2B (B2)
unnamed: MSMOT1.1, U3.MS3
unnamed: MSMOT1.2, U3.MS2
unnamed: MSMOT1.3, U3.MS1
unnamed: U4.RST, U4.SLP
unnamed: C13.2, U2.9 (R2OUT)
unnamed: MSMOT2.1, U4.MS3
unnamed: MSMOT2.2, U4.MS2
unnamed: MSMOT2.3, U4.MS1
unnamed: MOT2.1, U4.1A (A1)
unnamed: MOT2.2, U4.2A (A2)
unnamed: MOT2.3, U4.1B (B1)
unnamed: MOT2.4, U4.2B (B2)
unnamed: RS232.2, U2.14 (T1OUT)
unnamed: RS232.3, U2.13 (R1IN)
unnamed: C9.+, U2.1 (C1+)
unnamed: C9.-, U2.3 (C1-)
unnamed: C10.+, U2.4 (C2+)
unnamed: C10.-, U2.5 (C2-)
unnamed: C11.+, U2.2 (V+)
unnamed: C12.-, U2.6 (V-)
unnamed: RS232.4, U2.8 (R2IN)
unnamed: R2.1, U5.CH_PD
unnamed: R4.2, T1.2 (B)
unnamed: R3.2, T1.3 (C)
unnamed: IROUT.1, T1.1 (E)
unnamed: IC3.1 (OUT), R15.1, U1.28 (PC5(ADC5/SCL))
unnamed: D1.A, T2.1 (E)
unnamed: R10.2, T2.2 (B)
unnamed: R11.2, T2.3 (C)
unnamed: ENDSTOP.3, R12.2
unnamed: ENDSTOP.2, IC3.2 (-IN)
unnamed: IC3.3 (+IN), R14.1, R15.2, R16.S
unnamed: R4.1, U1.14 (PB0(ICP))
unnamed: C18.1, Q1.2, U1.10 (PB7(XTAL2/TOSC2))
unnamed: C17.1, Q1.1, U1.9 (PB6(XTAL1/TOSC1))
unnamed: D2.A, JP1.PWR
RESET: C13.1, ICSP.5, R1.2, RESET.3, RESET.4 (P1), U1.1 (PC6(/RESET))
RIGHT: R7.1, RIGHT.1 (S), RIGHT.2 (S1), U1.13 (PD7(AIN1))
RXD: U1.4 (PD2(INT0)), U2.12 (R1OUT)
SCK: ICSP.3, U1.19 (PB5(SCK))
STATUS: R10.1, U1.16 (PB2(SS/OC1B))
STEP1: U1.25 (PC2(ADC2)), U3.STEP
STEP2: U1.27 (PC4(ADC4/SDA)), U4.STEP
TILTCCW: R8.1, TILTCCW.1 (S), TILTCCW.2 (S1), U1.12 (PD6(AIN0))
TILTCW: R6.1, TILTCW.1 (S), TILTCW.2 (S1), U1.15 (PB1(OC1A))
TXD: U1.5 (PD3(INT1)), U2.11 (T1IN)

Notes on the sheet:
Reset on DTR Signal to reset µC on new Connection
Place near µC Power Pins

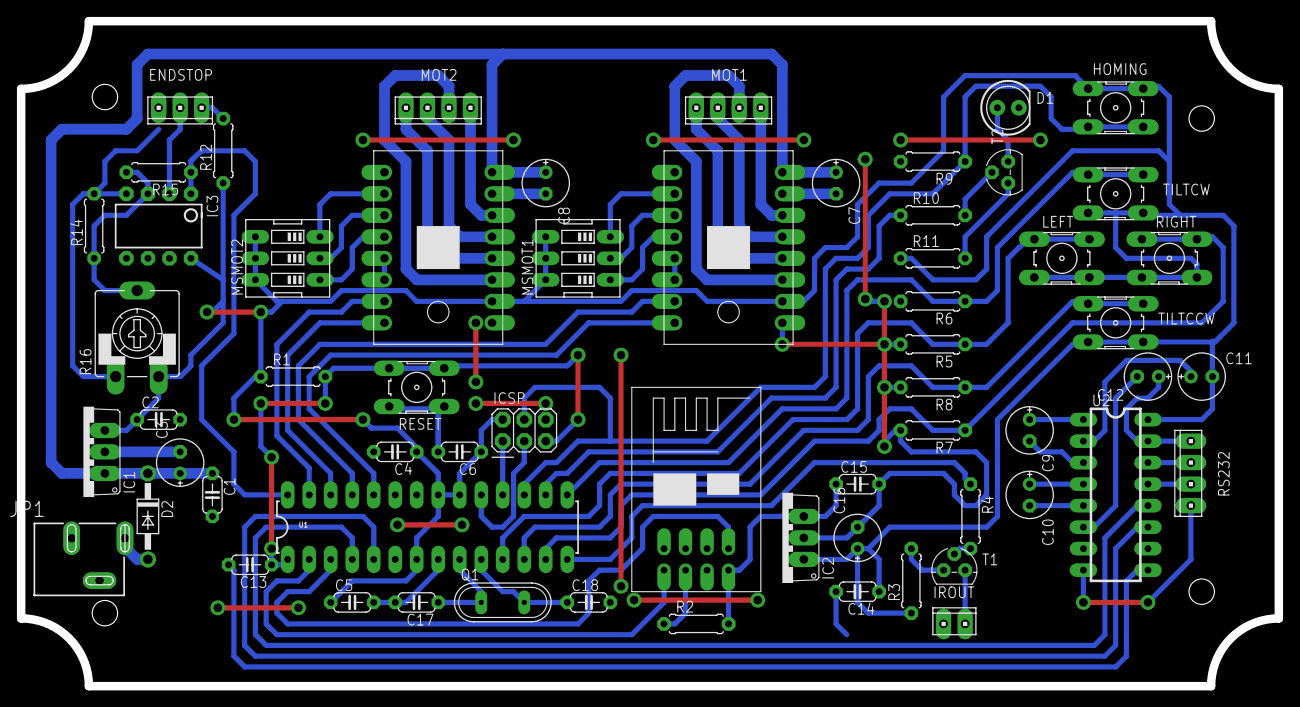
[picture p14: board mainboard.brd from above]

Board: 2 copper layers, 148.5 x 78.5 mm, 61 parts (0 on the bottom side), 62 nets.

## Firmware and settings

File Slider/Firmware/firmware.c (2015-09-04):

#include <stdbool.h>
#include <stdlib.h>
#include <string.h>

#include <util/delay.h>
#include <avr/interrupt.h>
#include <avr/io.h>

#include "constants.h"

#include "uart.h"
#include "timer.h"
#include "software_uart.h"

#define __LOGARITHMIC_SPEED__ 1

volatile uint32_t speedLinear = 0;
volatile uint32_t speedAngular = 0;

volatile int32_t stepCounterLinear = 0;
volatile int32_t stepCounterAngular = 0;

volatile uint32_t sendPositionDebounceCounter = 0;

volatile bool linearDirection = DIR_LEFT; 
volatile bool angularDirection = DIR_CW; 

volatile bool linearStopped = false; 
volatile bool angularStopped = false; 

void gpioInit()
{
    // save set all DDRs to a known state
    DDRB = 0x00;
    DDRC = 0x00;
    DDRD = 0x00;

    // set all pin DDRs
    SET(IR_DDR, IR_PIN); // set IR TRANSMITTER as output
    SET(LED_DDR, LED_PIN); // set status LED as output
    SET(SOFT_UART_DDR, SOFT_UART_TX_PIN); // set TXD as output

    SET(MOTOR_DRIVER_DDR, ANGULAR_DIR_PIN); // set DIR1 as output
    SET(MOTOR_DRIVER_DDR, ANGULAR_STEP_PIN); // set STEP1 as output
    SET(MOTOR_DRIVER_DDR, LINEAR_DIR_PIN); // set DIR2 as output
    SET(MOTOR_DRIVER_DDR, LINEAR_STEP_PIN); // set STEP2 as output

    CLEAR(BUTTON_LEFT_DDR, BUTTON_LEFT_PIN); // set LEFT as input
    CLEAR(BUTTON_RIGHT_DDR, BUTTON_RIGHT_PIN); // set RIGHT as input
    CLEAR(BUTTON_CCW_DDR, BUTTON_CCW_PIN); // set CCW as input
    CLEAR(BUTTON_CW_DDR, BUTTON_CW_PIN); // set CW button as input
    CLEAR(BUTTON_HOMING_DDR, BUTTON_HOMING_PIN); // set HOMING as input
    CLEAR(ENDSTOP_TRIGGER_DDR, ENDSTOP_TRIGGER_PIN); // set ENDSTOP as input
}

void doLinearStep(uint8_t dir)
{
    //increment or decrement the step counter
    dir ? stepCounterLinear++ : stepCounterLinear--;

    //set the dir pin to the direction
    VALUE(MOTOR_DRIVER_PORT, LINEAR_DIR_PIN, dir);

    //set the step pin high
    SET(MOTOR_DRIVER_PORT, LINEAR_STEP_PIN);

    //wait a millisecond
    _delay_ms(6);

    //set the step count back low
    CLEAR(MOTOR_DRIVER_PORT, LINEAR_STEP_PIN);

    //wait another millisecond
    _delay_ms(6);
}
void doAngularStep(uint8_t dir)
{
    //increment or decrement the step counter
    dir ? stepCounterAngular++ : stepCounterAngular--;

    //set the dir pin to the direction
    VALUE(MOTOR_DRIVER_PORT, ANGULAR_DIR_PIN, dir);

    //set the step pin high
    SET(MOTOR_DRIVER_PORT, ANGULAR_STEP_PIN);

    //wait a millisecond
    _delay_ms(6);

    //set the step count back low
    CLEAR(MOTOR_DRIVER_PORT, ANGULAR_STEP_PIN);

    //wait another millisecond
    _delay_ms(6);
}

void homeLinear(){
	while(stepCounterLinear != 0){
		uint8_t dir = stepCounterLinear > 0 ? DIR_RIGHT : DIR_LEFT;
		doLinearStep(dir);
	}
}

void homeAngular(){
	while(stepCounterAngular != 0){
		uint8_t dir = stepCounterAngular > 0 ? DIR_CW : DIR_CCW;
		doAngularStep(dir);
	}
}

void timerElapsed()
{
    static uint8_t timeoutCounterLinear = 0;
    static uint8_t timeoutCounterAngular = 0;

    timeoutCounterAngular++;
    //each time we increment the move counter by 2, so it is twice as fast as the angular rotation
    timeoutCounterLinear += 4;
    sendPositionDebounceCounter++;

    if (timeoutCounterLinear >= speedLinear && !linearStopped) {

        //set the direction pin
        VALUE(MOTOR_DRIVER_PORT, LINEAR_DIR_PIN, linearDirection);

        timeoutCounterLinear = 0;
        //increment step counter because we're going to perform a step
        linearDirection ? stepCounterLinear++ : stepCounterLinear--;
        // set move pin high, to perform a step
        SET(MOTOR_DRIVER_PORT, LINEAR_STEP_PIN);
    }
    else {
        // set step pin low again to be ready for the next step
        CLEAR(MOTOR_DRIVER_PORT, LINEAR_STEP_PIN);
    }

    if (timeoutCounterAngular >= speedAngular && !angularStopped) {

        //set the direction pin
        VALUE(MOTOR_DRIVER_PORT, ANGULAR_DIR_PIN, angularDirection);

        timeoutCounterAngular = 0;
        //increment step counter because we're going to perform a step
        angularDirection ? stepCounterAngular++ : stepCounterAngular--;
        // set rotate pin high to do a step
        SET(MOTOR_DRIVER_PORT, ANGULAR_STEP_PIN);
    }
    else {
        // set step pin low again to be ready for the next step
        CLEAR(MOTOR_DRIVER_PORT, ANGULAR_STEP_PIN);
    }
}

void handleUI()
{
    if (ISSET(BUTTON_LEFT_PORT, BUTTON_LEFT_PIN)) { // if left pressed
        SET(LED_PORT, LED_PIN); // switch on LED while button is pressed
        doLinearStep(DIR_LEFT);
    }
    else if (ISSET(BUTTON_RIGHT_PORT, BUTTON_RIGHT_PIN)) { // if right pressed
        SET(LED_PORT, LED_PIN); // switch on LED while button is pressed
        doLinearStep(DIR_RIGHT);
    }
    else if (ISSET(BUTTON_CCW_PORT, BUTTON_CCW_PIN)) { // if ccw pressed
        SET(LED_PORT, LED_PIN); // switch on LED while button is pressed
        doAngularStep(DIR_CCW);
    }
    else if (ISSET(BUTTON_CW_PORT, BUTTON_CW_PIN)) { // if cw pressed
        SET(LED_PORT, LED_PIN); // switch on LED while button is pressed
        doAngularStep(DIR_CW);
    }
    else if (PINC >> PC5) { // endstop triggered

        SET(LED_PORT, LED_PIN); // LED on
    }
    else {
        CLEAR(IR_PORT, IR_PIN); // switch off IR output driver
        CLEAR(LED_PORT, LED_PIN); // switch off LED
    }
}

int speedStringToSpeed(char* speedString){
    return 270 - strtol(speedString, NULL, 16);
}

void handleUartMessages()
{
    if (uartAvailable()) {
        char line[RX_BUFF];
        uartReadLine(line);

        if (line[0] == 'M') {
        	//handle move messages
            if (line[1] == '+') {
            	//positive direction -> DIR_RIGHT
                linearStopped = false;
                linearDirection = DIR_RIGHT;
                speedLinear = speedStringToSpeed(line + 2);
            }
            else if (line[1] == '-') {
                linearStopped = false;
                linearDirection = DIR_LEFT;
                speedLinear = speedStringToSpeed(line + 2);
            }
            else if (line[1] == '0') {
                linearStopped = true;
            }
        }
        else if (line[0] == 'R') {
        	//handle rotation messages
            if (line[1] == '+') {
            	//positive direction -> DIR_CW
                angularStopped = false;
                angularDirection = DIR_CW;
                speedAngular = speedStringToSpeed(line + 2);
            }
            else if (line[1] == '-') {
                angularStopped = false;
                angularDirection = DIR_CCW;
                speedAngular = speedStringToSpeed(line + 2);
            }
            else if (line[1] == '0') {
                angularStopped = true;
            }
        }
        else if(line[0] == 'H'){
        	//handle HOMING
        	if(line[1] == 'M'){
        		homeLinear();
        	}else if(line[1] == 'R'){
        		homeAngular();
        	}
        }else if(line[0] == 'Z'){
        	//handle rereference
        	if(line[1] == 'M'){
        		stepCounterLinear = 0;
        	}else if(line[1] == 'R'){
        		stepCounterAngular = 0;
        	}
        }
    }
}

void handleHardcodedScript()
{
    static bool running = false;
    static uint8_t totalSteps = 0;

    if (ISSET(BUTTON_HOMING_PORT, BUTTON_HOMING_PIN)) { // start the script if the
        // homing button was
        // pressed
        running = true; // start the script
    }

    // check if the script was started
    if (running) {
        SET(LED_PORT, LED_PIN); // LED on

        if (totalSteps % 12 == 0) {
            doAngularStep(DIR_CW);
        }

        doLinearStep(DIR_LEFT);

        totalSteps++;

        _delay_ms(100);
    }
}

void checkPositionAndSendUpdate(){
    static int lastStepCountLinear = 0;
    static int lastStepCountAngular = 0;

    if(lastStepCountAngular != stepCounterAngular){
        char* message = "PR0000";
        if(stepCounterAngular <= 0xFFFF){
            //write the speed to the buffer at offset 2
            itoa(stepCounterAngular, message + 2, 16);
        
            uartWriteLine(message);
            lastStepCountAngular = stepCounterAngular;
        }
    }

    if(lastStepCountLinear != stepCounterLinear){
        char* message = "PM0000";
        if(stepCounterLinear <= 0xFFFF){
            //write the speed to the buffer at offset 2
            itoa(stepCounterLinear, message + 2, 16);
        
            uartWriteLine(message);
            lastStepCountLinear = stepCounterLinear;
        }
        lastStepCountLinear = stepCounterLinear;
    }
}

int main()
{
    // setup GPIO functions
    gpioInit();

    // register timer callback and start timer
    timerInit(timerElapsed);

    // setup hardware UART
    uartInit();
    
    // mainloop
    while (true) {
        handleUI();

        handleUartMessages();

        handleHardcodedScript();
        if(sendPositionDebounceCounter >= POSITION_DEBOUNCE_DELAY){   
            checkPositionAndSendUpdate();
            sendPositionDebounceCounter = 0;
        }
    }

    return 0;
}

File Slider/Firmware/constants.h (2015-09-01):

#ifndef __CONSTANTS_H__
#define __CONSTANTS_H__

#include <avr/io.h>

/********************************/
/*        HELPER MACROS         */
/********************************/
#define SET(PORT,PIN) ((PORT) |= ((1) << (PIN)))
#define CLEAR(PORT,PIN) ((PORT) &= ~((1) << (PIN)))
#define TOGGLE(PORT,PIN) ((PORT) ^= ((1) << (PIN)))
#define ISSET(PORT, PIN) (((PORT) >> (PIN)) & (1))
#define VALUE(PORT, PIN, STATUS) (PORT) = (PORT) & ~((uintmax_t)(1) << (PIN)) | ((uintmax_t)(STATUS) << (PIN))

/********************************/
/*     VARIOUS DEFINITIONS      */
/*       FOR READABILITY        */
/********************************/
#define DIR_LEFT 1
#define DIR_RIGHT 0
#define DIR_CW 0
#define DIR_CCW 1

#define POSITION_DEBOUNCE_DELAY 100 //send positions every x microseconds

/********************************/
/*       SOFTWARE UART          */
/********************************/
#define SOFT_UART_BAUD_RATE 9600
#define SECONDS_TO_MICROSECONDS 1000000
#define SOFT_UART_BITTIME (SECONDS_TO_MICROSECONDS / SOFT_UART_BAUD_RATE) // 1/9600 BAUD = 104µS

/********************************/
/*       PIN DEFINITIONS        */
/********************************/

/************ OUTPUTS ***********/

#define MOTOR_DRIVER_PORT PORTC
#define MOTOR_DRIVER_DDR DDRC
#define LINEAR_DIR_PIN PC1
#define ANGULAR_DIR_PIN PC3
#define LINEAR_STEP_PIN PC2
#define ANGULAR_STEP_PIN PC4

#define LED_PORT PORTB
#define LED_DDR DDRB
#define LED_PIN PB2

#define IR_PORT PORTB
#define IR_DDR DDRB
#define IR_PIN PB0

#define SOFT_UART_PORT PORTD
#define SOFT_UART_DDR DDRD
#define SOFT_UART_TX_PIN PD3

/************* INPUTS ***********/

#define BUTTON_LEFT_PORT PIND
#define BUTTON_LEFT_DDR DDRD
#define BUTTON_LEFT_PIN PD5

#define BUTTON_RIGHT_PORT PIND
#define BUTTON_RIGHT_DDR DDRD
#define BUTTON_RIGHT_PIN PD7

#define BUTTON_CCW_PORT PIND
#define BUTTON_CCW_DDR DDRD
#define BUTTON_CCW_PIN PD6

#define BUTTON_CW_PORT PINB
#define BUTTON_CW_DDR DDRB
#define BUTTON_CW_PIN PB1

#define BUTTON_HOMING_PORT PINB
#define BUTTON_HOMING_DDR DDRB
#define BUTTON_HOMING_PIN PB3

#define ENDSTOP_TRIGGER_PORT PINC
#define ENDSTOP_TRIGGER_DDR DDRC
#define ENDSTOP_TRIGGER_PIN PC5

#endif //__CONSTANTS_H__

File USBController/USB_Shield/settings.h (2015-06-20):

/* Copyright (C) 2011 Circuits At Home, LTD. All rights reserved.

This software may be distributed and modified under the terms of the GNU
General Public License version 2 (GPL2) as published by the Free Software
Foundation and appearing in the file GPL2.TXT included in the packaging of
this file. Please note that GPL2 Section 2[b] requires that all works based
on this software must also be made publicly available under the terms of
the GPL2 ("Copyleft").

Contact information
-------------------

Circuits At Home, LTD
Web      :  http://www.circuitsathome.com
e-mail   :  support@circuitsathome.com
 */

#ifndef USB_HOST_SHIELD_SETTINGS_H
#define USB_HOST_SHIELD_SETTINGS_H
#include "macros.h"

////////////////////////////////////////////////////////////////////////////////
// DEBUGGING
////////////////////////////////////////////////////////////////////////////////

/* Set this to 1 to activate serial debugging */
#define ENABLE_UHS_DEBUGGING 0

/* This can be used to select which serial port to use for debugging if
 * multiple serial ports are available.
 * For example Serial3.
 */
#ifndef USB_HOST_SERIAL
#define USB_HOST_SERIAL 0x0
#endif

////////////////////////////////////////////////////////////////////////////////
// Manual board activation
////////////////////////////////////////////////////////////////////////////////

/* Set this to 1 if you are using an Arduino Mega ADK board with MAX3421e built-in */
#define USE_UHS_MEGA_ADK 0 // If you are using Arduino 1.5.5 or newer there is no need to do this manually

/* Set this to 1 if you are using a Black Widdow */
#define USE_UHS_BLACK_WIDDOW 0

/* Set this to a one to use the xmem2 lock. This is needed for multitasking and threading */
#define USE_XMEM_SPI_LOCK 0

////////////////////////////////////////////////////////////////////////////////
// Wii IR camera
////////////////////////////////////////////////////////////////////////////////

/* Set this to 1 to activate code for the Wii IR camera */
#define ENABLE_WII_IR_CAMERA 0

////////////////////////////////////////////////////////////////////////////////
// MASS STORAGE
////////////////////////////////////////////////////////////////////////////////
// <<<<<<<<<<<<<<<< IMPORTANT >>>>>>>>>>>>>>>
// Set this to 1 to support single LUN devices, and save RAM. -- I.E. thumb drives.
// Each LUN needs ~13 bytes to be able to track the state of each unit.
#ifndef MASS_MAX_SUPPORTED_LUN
#define MASS_MAX_SUPPORTED_LUN 8
#endif

////////////////////////////////////////////////////////////////////////////////
// Set to 1 to use the faster spi4teensy3 driver.
////////////////////////////////////////////////////////////////////////////////
#ifndef USE_SPI4TEENSY3
#define USE_SPI4TEENSY3 0
#endif

////////////////////////////////////////////////////////////////////////////////
// AUTOMATIC Settings
////////////////////////////////////////////////////////////////////////////////

// No user serviceable parts below this line.
// DO NOT change anything below here unless you are a developer!

#include "version_helper.h"

#if defined(__GNUC__) && defined(__AVR__)
#ifndef GCC_VERSION
#define GCC_VERSION (__GNUC__ * 10000 + __GNUC_MINOR__ * 100 + __GNUC_PATCHLEVEL__)
#endif
#if GCC_VERSION < 40602 // Test for GCC < 4.6.2
#ifdef PROGMEM
#undef PROGMEM
#define PROGMEM __attribute__((section(".progmem.data"))) // Workaround for http://gcc.gnu.org/bugzilla/show_bug.cgi?id=34734#c4
#ifdef PSTR
#undef PSTR
#define PSTR(s) (__extension__({static const char __c[] PROGMEM = (s); &__c[0];})) // Copied from pgmspace.h in avr-libc source
#endif
#endif
#endif
#endif

#if !defined(DEBUG_USB_HOST) && ENABLE_UHS_DEBUGGING
#define DEBUG_USB_HOST
#endif

#if !defined(WIICAMERA) && ENABLE_WII_IR_CAMERA
#define WIICAMERA
#endif

// To use some other locking (e.g. freertos),
// define XMEM_ACQUIRE_SPI and XMEM_RELEASE_SPI to point to your lock and unlock.
// NOTE: NO argument is passed. You have to do this within your routine for
// whatever you are using to lock and unlock.
#if !defined(XMEM_ACQUIRE_SPI)
#if USE_XMEM_SPI_LOCK || defined(USE_MULTIPLE_APP_API)
#include <xmem.h>
#else
#define XMEM_ACQUIRE_SPI() (void(0))
#define XMEM_RELEASE_SPI() (void(0))
#endif
#endif

#if !defined(EXT_RAM) && defined(EXT_RAM_STACK) || defined(EXT_RAM_HEAP)
#include <xmem.h>
#else
#define EXT_RAM 0
#endif

#if defined(CORE_TEENSY) && (defined(__MK20DX128__) || defined(__MK20DX256__))
#define USING_SPI4TEENSY3 USE_SPI4TEENSY3
#else
#define USING_SPI4TEENSY3 0
#endif

#if ((defined(ARDUINO_SAM_DUE) && defined(__SAM3X8E__)) || defined(RBL_NRF51822) || defined(__ARDUINO_X86__) || ARDUINO >= 10600) && !USING_SPI4TEENSY3
#include <SPI.h> // Use the Arduino SPI library for the Arduino Due, RedBearLab nRF51822, Intel Galileo 1 & 2, Intel Edison or if the SPI library with transaction is available
#endif
#if defined(__PIC32MX__) || defined(__PIC32MZ__)
#include <../../../../hardware/pic32/libraries/SPI/SPI.h> // Hack to use the SPI library
#endif
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

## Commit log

2015-04-04 added CAD drawings
    - added motor plate
    - added gear plate
    - added camera plate
    - added camera plate (bottom part)
    - added x axis sled
    [Drehtellerbefestigung oben.dwg, Drehtellerbefestigung unten.dwg, Kamerabefestigung.dwg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]
2015-04-24 added CAD drawing for Motorshaftcoupling
    [Motorplattenbefestigung.dwg]
2015-04-25 Added firmware framework
2015-04-25 Added mainboard scheme with basic ABR setup
    [mainboard.brd, mainboard.sch]
2015-05-04 added SocketRocket dependency
2015-05-04 implement basic slider, reworked record button
2015-05-05 added Web Socket Mock server
2015-05-15 refactorec connectionManager to CameraControl Object
2015-05-15 Added Motor Drivers, Serial Interface and ICSP Header to schematic
    [mainboard.sch]
2015-05-16 Completed schematic
    - added endstop amplifier
    - added user interface (switches for manual control)
    - added IR emitter circuit
    - created wifi module
    - added 3.3V rail
    - moved debug serial port to PD2 and PD3 (software emulated)
    [mainboard.brd, mainboard.sch]
2015-05-16 small relayout of the schematic
    no functional changes
    [mainboard.sch]
2015-05-16 added 16 MHZ Crystal with throughhole footprint
    [mainboard.sch]
2015-05-16 small relayouting
    [mainboard.sch]
2015-05-16 moved group designators to modules layer
    [mainboard.sch]
2015-05-16 adjustments in layout and endstop amp
    - added adjustable resistor to voltage divider on positive opamp input in endstop amp to allow adjustment of triggerpoint
    - some layout fixes
    [mainboard.sch]
2015-05-18 added board layout file with presorted module components
    [mainboard.brd, mainboard.sch]
2015-05-18 Started layouting seperate modules
    [mainboard.brd, mainboard.sch]
2015-05-19 Further board layouting
    [mainboard.brd, mainboard.sch]
2015-05-22 progress in board layout and schematic
    - fixed the layout of the schematic after pin swapping
    - board connections all done
    - board layout all done
    - adjusted outline to match case
    [mainboard.brd, mainboard.sch]
2015-05-22 switched from generic pinheaders to the right connector footprint
    [mainboard.brd, mainboard.sch]
2015-06-01 added milling layer to board
    [mainboard.brd, mainboard.sch]
2015-06-16 Added first version of the USB Controller files.
    Will be refactored in further release to be more
    independet from arduino based code but runs already
    independently from the arduino IDE in pure c/c++.
2015-06-20 added LCD Font view Library and first implementation of the timer view
2015-06-23 added code for pan movement buttons
2015-06-30 added uart functions and simple parsing of the mesage format
2015-07-21 added switchable slider movement control
2015-08-16 finished up live controller - cleaned up autolayout - added speed view - added homing butons - seperated controls and info view
2015-08-22 Color Scriptcontrol Buttons
2015-08-28 renamed drawings to english names
    [camera attachment.dwg, motor attachment.dwg, motorplate attachment.dwg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]
2015-09-01 linked pdfs to schematic images
2015-09-01 refactored firmware and added functions for sending websocket messages over uart
2015-09-01 added link to black/white schematic for etching
2015-09-04 Fixed firmware bugs and some styling changes in xcode
    [firmware.c]

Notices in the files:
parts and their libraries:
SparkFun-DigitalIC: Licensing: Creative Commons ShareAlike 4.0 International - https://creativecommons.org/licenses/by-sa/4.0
